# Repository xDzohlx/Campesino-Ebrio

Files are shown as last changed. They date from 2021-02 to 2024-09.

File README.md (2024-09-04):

# Campesino-Ebrio Robot de combate de 12 lb. 

Este es el robot mas completo que he desarrollado.

Ha competido en 4 competencias y actualmente es la versión 3 del robot.

Talent land 2019
Primer competencia del campesino
Tryta 2019
Al no recibir mucho daño tecnicamente se volvio a construir y volvio a competir
Motorama robot conflict 2020
Subcampeon del torneo y primer evento internacional donde se compitió
Norwalk Havoc Robot League 6 feb 2021
Tercer lugar de 4 robots inscritos no se tuvo muy buen desempeño
Norwalk Havoc Robot League Junio 2021
Norwalk Havoc Robot League Finalist Diciembre 2021
Motorama Robot Conflict 2022
Norwalk Havoc Robot League Octubre 2023

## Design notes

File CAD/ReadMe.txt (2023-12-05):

No avanzar los estados de reconstrucción. 
A veces la polea grande no se reconstruye correctamente.

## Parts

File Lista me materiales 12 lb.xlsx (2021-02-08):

Parte | Descripcion | Cantidad | Enlace
Motor del arma | Motor de alta velocidad y potencia | 1 | https://hobbyking.com/es_es/turnigy-xk-3665-3190kv-brushless-inrunner.html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
Motor traccion | Motores de baja velocidad y potencia moderada | 2 | https://hobbyking.com/es_es/propdrive-v2-3536a-910kv-brushless-outrunner-motor.html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
Controladora arma | Controladora de alta corriente | 1 | https://hobbyking.com/es_es/turnigy-plush-32-100a-2-6s-speed-controller-w-bec.html
Controladora traccion | Controladora Bheli32 | 1 | https://hobbyking.com/es_es/flycolor-x-cross-bl-32-50a-brushless-esc.html
Bateria | Bateria lipo de 1300mAmp 4s | 2~3 | https://www.agelectronica.com/detalle.php?p=TA-45C-1300-4S1P-XT60
Radio | Clasico i6 | 1 | https://hobbyking.com/es_es/turnigy-tgy-i6-mode-2-afhds-transmitter-and-6ch-receiver.html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
Switch de encedido | Switch fingertech para traccion y radio | 2 | https://www.fingertechrobotics.com/proddetail.php?prod=ft-mini-switch
Cajas de reduccion | Clasicas p60 de banebots | 2 | http://www.banebots.com/product/P61S-44.html
Ruedas | Colson de 4x1/4 | 2 | http://www.banebots.com/product/WC2-4.html

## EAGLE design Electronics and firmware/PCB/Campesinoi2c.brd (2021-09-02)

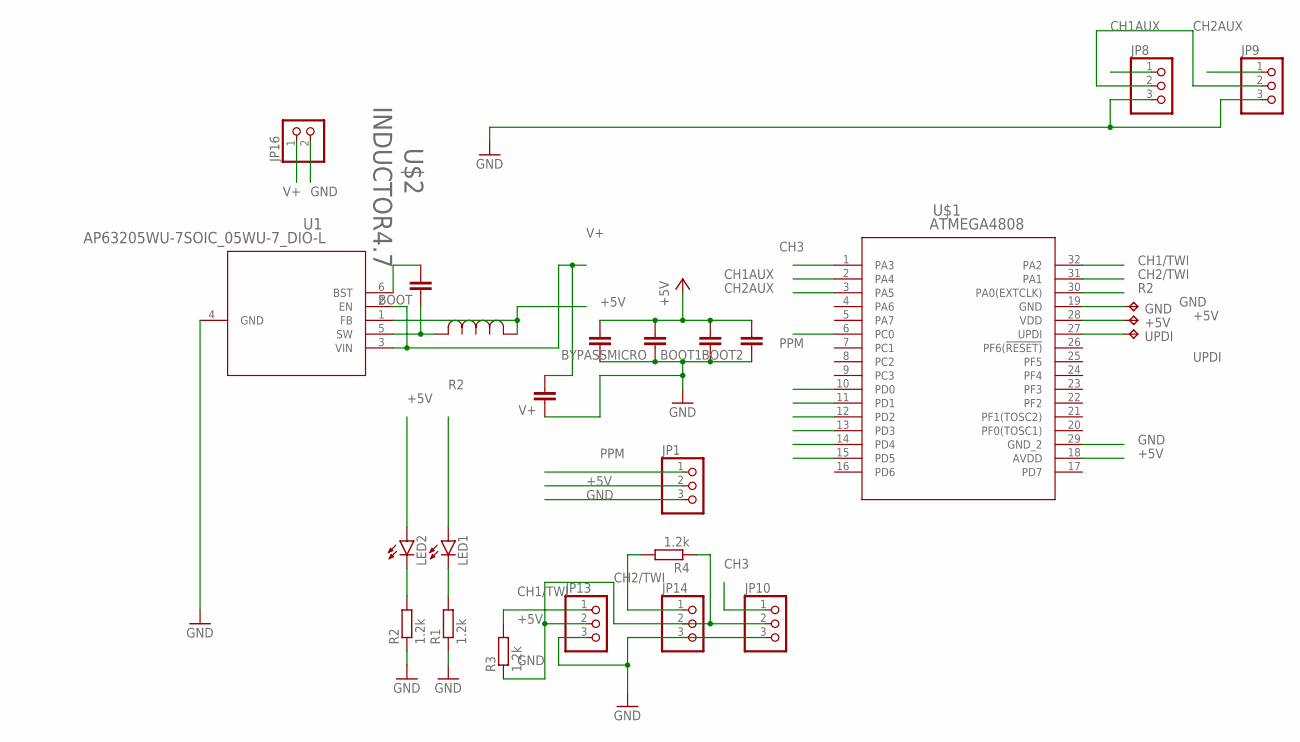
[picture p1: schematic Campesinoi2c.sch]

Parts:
+5V: TPB1,27; B1,27
BOOT, BOOT1, BOOT2: C-EUC0402; C0402
BYPASSMICRO, BYPASSMICRO2: C-EUC0603; C0603
GND: TPB1,27; B1,27
JP1, JP8, JP9, JP10, JP13, JP14: PINHD-1X03_2.54-S; 1X03-S
JP16: PINHD-1X02_2.54-S; 1X02-S
LED1, LED2: LEDCHIPLED_0603; CHIPLED_0603
R1, R2, R3, R4: 1.2k; R0603
U1: AP63205WU-7SOIC_05WU-7_DIO-L; SOIC_05WU-7_DIO-L
U$1: ATMEGA4808; QFP80P900X900X120-32N
U$2: INDUCTOR4.7; IND_NRS5030T100MMGJ_TAY
UPDI: TPB1,27; B1,27
V+: C-EUC1206; C1206

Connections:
+5V: +5V.TP, BOOT1.2, BOOT2.2, BYPASSMICRO.2, BYPASSMICRO2.2, JP1.2, JP8.2, JP9.2, JP10.2, JP13.2, JP14.2, LED2.A, R3.1, R4.1, U1.1 (FB), U$1.18 (AVDD), U$1.28 (VDD), U$2.1
CH1/TWI: JP13.1, R3.2, U$1.32 (PA2)
CH1AUX: JP8.1, U$1.2 (PA4)
CH2/TWI: JP14.1, R4.2, U$1.31 (PA1)
CH2AUX: JP9.1, U$1.3 (PA5)
CH3: JP10.1, U$1.1 (PA3)
GND: BOOT1.1, BOOT2.1, BYPASSMICRO.1, BYPASSMICRO2.1, GND.TP, JP1.3, JP8.3, JP9.3, JP10.3, JP13.3, JP14.3, JP16.2, R1.1, R2.1, U1.4 (GND), U$1.19 (GND), U$1.29 (GND_2), V+.1
unnamed: LED2.C, R2.2
unnamed: LED1.C, R1.2
unnamed: BOOT.1, U1.5 (SW), U$2.2
unnamed: BOOT.2, U1.6 (BST)
PPM: JP1.1, U$1.6 (PC0)
R2: LED1.A, U$1.30 (PA0(EXTCLK))
SENSOR1: U$1.10 (PD0)
SENSOR2: U$1.11 (PD1)
SENSOR3: U$1.12 (PD2)
SENSOR4: U$1.13 (PD3)
SENSOR5: U$1.14 (PD4)
SENSOR6: U$1.15 (PD5)
UPDI: U$1.27 (UPDI), UPDI.TP
V+: JP16.1, U1.2 (EN), U1.3 (VIN), V+.2

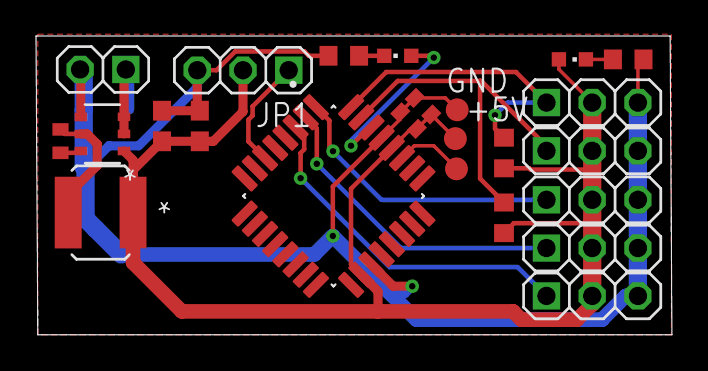
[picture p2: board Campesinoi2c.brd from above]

Board: 2 copper layers, 35.3 x 16.6 mm, 25 parts (1 on the bottom side), 15 nets.

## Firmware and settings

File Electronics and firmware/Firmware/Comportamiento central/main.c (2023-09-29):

/*
	 * Comportamiento central.c
	 *
	 * Created: 06/07/2021 19:38:21
	 * Author : xDzohlx
	 */ 

	#define F_CPU 16000000UL //Frecuencia del cpu 16 MHz
	#define USART0_BAUD_RATE(BAUD_RATE) ((float)(F_CPU * 32 / (16 * (float)BAUD_RATE)) + 0.5)
	#define Kp 32
	#define D 10
	#define acelerador 1
	#define volante 0
	#define arma 3
	#define izquierdo 0
	#define derecho 1
	#define sensor_reversa 4
	#define sensor_acelerometro 5
	#define controlador 3

	#include <avr/io.h>
	#include <avr/interrupt.h>
	#include <avr/cpufunc.h>
	#include <stdbool.h>
	#include <util/delay.h>
	#include <stdio.h>
	
	#define TCB_CMP_EXAMPLE_VALUE   (0x80FF)
	
	void USART0_init(void);
	char USART0_readChar(void);
	//uint8_t softwareid  __attribute__ ((.noinit)) = 0x01;


	uint8_t cont = 0;//Contador de canal
	uint8_t contadc = 0;//Contador de sensores
	uint8_t contador = 0;
	uint8_t programa = 0;
	//uint8_t contfiltro=0;
	
	uint16_t Controlador_D[2] ;
	uint16_t Controlador_P[2] ;
	uint16_t error_anterior = 0;
	volatile uint16_t VALORADC = 0x0000;
	volatile uint16_t canal[7];//valor de canal de 4000 hasta 8000
	//uint16_t canalcal[3][7];//vectores de calibracion
	//uint16_t sensorcal[3][7];
	volatile static uint16_t canalcontrol[2];
	volatile uint16_t sensor[16];
	volatile uint16_t motor[2];//motor 0 izquid, motor 1 derecho
	volatile uint16_t automatico[2];
	volatile uint16_t motor_arma = 0x0000;
	volatile uint8_t contador_pwm_alto = 0x00;
	//volatile uint8_t contador_pwm_bajo = 0x00;
	//RC canales SBUS
	
	volatile static uint8_t sbuschannel[25];
	volatile static uint8_t sbuschannelindex = 0;
	volatile static uint8_t buffer_sbus = 0x00;
	volatile static uint8_t sbus_anterior = 0x00;
	volatile static uint16_t nuevo_canal[25];
	volatile static bool activar_pwm = false;
	
	
	uint16_t controlautomatico[2];
	uint16_t controlautomaticoprevio[2];
	uint16_t canaloffset[2];
	uint16_t sensoroffset[8];
	uint16_t millis[3];
	uint16_t previousmillis = 0;
	uint16_t currentmillis = 0;
	uint16_t nuevomillis = 0;
	uint8_t contfiltro = 0x00;
	uint8_t numsensor = 0;
	char dato_uart = 0x00;
	volatile uint8_t sensorcontrol[2];
	volatile bool manual = true;//0 sin asistencia, 1 asistencia, 2 autonomo
	volatile bool asistido = false;
	volatile bool autonomo = false;
	bool lectura = false;
	bool lectura_canal = false;
	bool sentido = false;
	bool finadelante = false;
	bool fingiro = false;
	volatile bool primero = true;
	volatile bool segundo = true;
	volatile bool tercero = true;
	bool cuarto = false;
	volatile bool reversa = false;
	volatile bool control_reversa = false;

	void offsetsignals(){//etapa de autocalibracion por promedio, pequeño filtro digital
	PORTA.DIRCLR = PIN0_bm;
	PORTF.OUTSET = PIN0_bm|PIN1_bm|PIN2_bm|PIN3_bm;
		while (!lectura_canal&&canal[acelerador]<6500&&canal[acelerador]>5500&&canal[volante]<6500&&canal[volante]>5500){//Seguridad
		}
		_delay_ms(1500);
		for (int i = 0;i<8;i++){//adquisición de señales, 8 valores en total
			_delay_ms(20);
			canaloffset[volante] += canal[volante];
			canaloffset[acelerador] += canal[acelerador];
			sensoroffset[sensor_acelerometro] += sensor[sensor_acelerometro];
		}
		sensoroffset[sensor_acelerometro] = (sensoroffset[sensor_acelerometro]>>3);
		canaloffset[volante] = (canaloffset[volante]>>3);//division del promedio
		canaloffset[acelerador] = (canaloffset[acelerador]>>3);
	PORTF.OUTCLR = PIN0_bm|PIN1_bm|PIN2_bm|PIN3_bm;
	PORTA.DIRSET = PIN0_bm;
	}
	//generador de trayectorias, falta el parametro de velocidad mientras tanto sera fija
	//valores de 4000 a 2000
	uint16_t adelante(uint16_t distancia, uint16_t velocidad){//control de aceleracion de 2000, 2000 max
		if (segundo){
			millis[acelerador] = 0;// reiniciar temporizador
			segundo = false;
		}
			if (millis[acelerador]<=velocidad){//rampa positiva
				controlautomatico[acelerador] = canaloffset[acelerador]+millis[acelerador];
				//controlautomaticoprevio[acelerador] = controlautomatico[acelerador];
			}
		if (millis[acelerador]>=(distancia<<1)){
				contador++;
				segundo = true;
		}
		return  controlautomatico[acelerador];
	}
	uint16_t giro(uint16_t distancia,uint16_t velocidad,bool sentido){//true derecha, false izquierda,alrededor de 900 son 90 grados con 550 de velcodiad tangencial y 500 de giro
				if (primero){
					millis[volante] = 0;// reiniciar temporizador
					primero = false;
				}
				if (millis[volante]>=(distancia)){
					if (controlautomatico[volante]<= canaloffset[volante]){//saturacion
						controlautomatico[volante] = canaloffset[volante];
						}else{
							if(sentido){
						controlautomatico[volante] = (controlautomaticoprevio[volante]<<1)-canaloffset[volante]-millis[volante];//rampa inversa
							}else{
						controlautomatico[volante] = (controlautomaticoprevio[volante]<<1)-canaloffset[volante]+millis[volante];//rampa inversa		
							}
					}
					}else{
					if (millis[volante]<=velocidad){//rampa positiva
						if (sentido){
						controlautomatico[volante] = canaloffset[volante]+millis[volante];
						} 
						else{
						controlautomatico[volante] = canaloffset[volante]-millis[volante];
						}
						controlautomaticoprevio[volante] = controlautomatico[volante];
					}
				}
				if (millis[volante]>=(distancia<<1)){
				controlautomatico[volante] = canaloffset[volante];
				contador++;
				primero = true;
				}
				return  controlautomatico[volante];
	}	
	void ocho(void){
		if (contador==0){
			canalcontrol[volante] = canaloffset[volante];
			canalcontrol[acelerador] = adelante(2000,500);
		}
		if (contador==1){
			canalcontrol[volante] = giro(910,500,false);
		}
		//if (contador==2){
			//canalcontrol[volante] = canaloffset[volante];
			//canalcontrol[acelerador] = adelante(450,450);
		//}
		//if (contador==3){
			//canalcontrol[volante] = giro(2000,500,false);
		//}
		if (contador>=2){
			contador = 0;
		}
	}
	void busqueda(void){
		if (contador==0){
			canalcontrol[volante] = canaloffset[volante];
			canalcontrol[acelerador] = adelante(1000,700);
		}
		if (contador==1){
			canalcontrol[volante] = giro(1200,100,true);
		}
		if (contador>=2){
			contador = 0;
		}
	}
	
	char USART0_readChar(void)
	{
		while (!(USART0.STATUS & USART_RXCIF_bm))
		{
			;
		}
		return USART0.RXDATAL;
	}
	
	void USART1_init(void)
	{
		//PORTA.DIR &= ~PIN1_bm;
		//PORTC.DIR |= PIN0_bm;
		
		USART1.BAUD = (uint16_t)USART0_BAUD_RATE(100000);

		USART1.CTRLA |= USART_RXCIE_bm;

		USART1.CTRLB |= USART_RXEN_bm;
		
		USART1.CTRLC |= USART_PMODE_EVEN_gc|USART_SBMODE_2BIT_gc;
	}
	
 void USART0_sendChar(char c)
	{
		while (!(USART0.STATUS & USART_DREIF_bm))
		{
			;
		}
		USART0.TXDATAL = c;
	}
	
void USART0_init(void)
{
	PORTA.DIR |= PIN0_bm;
	
	USART0.BAUD = (uint16_t)USART0_BAUD_RATE(9600);
	
	USART0.CTRLB |= USART_TXEN_bm;
	
}
	
	void setup(void){
	
		//Configuracion de CLKPER para fuente de reloj de varios perifericos
		ccp_write_io((void *) & (CLKCTRL.MCLKCTRLB), (CLKCTRL_PDIV_2X_gc|CLKCTRL_PEN_bm));//Maxima frecuencia de lectura de pwm en señal de reloj per
			//RTC Reloj de tiempo real
		//while((RTC.STATUS > 0x00 )){}//se checa que no se este uitilizando	el RTC
		//RTC.PER = 0x01A4;//Timer para apagar sistemas autonomos en 7 minutos
		//RTC.CLKSEL = RTC_CLKSEL_INT32K_gc;
		//RTC.DBGCTRL |= RTC_DBGRUN_bm;
		//RTC.CTRLA = RTC_PRESCALER_DIV32768_gc| RTC_RTCEN_bm| RTC_RUNSTDBY_bm;
		//RTC.INTCTRL |= RTC_OVF_bm;//RTC_CMP_bm;
		//configuracion de puertos
		
		PORTA.DIRSET = PIN0_bm|PIN1_bm|PIN0_bm|PIN2_bm|PIN3_bm;//PIN1_bm|PIN0_bm|PIN4_bm|PIN5_bm|PIN6_bm|PIN7_bm;//dirección de entrada en este caso es de salida
		//PORTA.DIRCLR = PIN1_bm;
		PORTF.DIRSET = PIN0_bm|PIN1_bm|PIN2_bm|PIN3_bm;
		
		
		//TCB0.CTRLA |= TCB_ENABLE_bm|TCB_CLKSEL_CLKDIV2_gc;//ACTIVACION DE EVENTOS RELOJ PROVIENE DE TCA A 1MHZ //clkper 
		//TCB0.CTRLB |= TCB_CNTMODE_FRQ_gc;//modo de lectura de frecuencia
		//TCB0.EVCTRL |= TCB_CAPTEI_bm|TCB_EDGE_bm;//ACTIVA CAPTURA DE EVENTOS, EDGE es el sentido del pulso en este caso esta inverso
		//TCB0.INTCTRL |= TCB_CAPT_bm;
		//TCB1.CTRLB |= 0;//modo de tiempo fuera

		TCB0.CTRLA |= TCB_ENABLE_bm;
		TCB0.CCMP = 0xFA0;//Valor top 4000 interrupcion cada milisegundo
		TCB0.INTCTRL |= TCB_CAPT_bm;//habilita la interrupcion	
		
	
		//Interrupcion para perifericos de baja velocidad
		TCB2.CTRLA |= TCB_ENABLE_bm|TCB_CLKSEL_CLKDIV2_gc;
		TCB2.CCMP = 0xFFFE;//Valor top 4000 interrupcion cada 10 milisegundos
		TCB2.INTCTRL |= TCB_CAPT_bm;//habilita la interrupcion
		//USART SBUS PARA RC
		USART0_init();
		USART1_init();
		//CONFIGURACION DE RED DE EVENTOS
		//Configuracion de sistema de eventos para el radio
		EVSYS.CHANNEL2 |= EVSYS_GENERATOR_PORT0_PIN0_gc;//PORTC0 CONECTADO A CANAL 2 para lectura de ppm
		
		EVSYS.USERTCB0 |= EVSYS_CHANNEL_CHANNEL2_gc;//usuario TCB0 conectado al canal 2
		//Configuracion de sistema de eventos para sensor de reversa con filtro
		EVSYS.CHANNEL0 |= EVSYS_GENERATOR_PORT0_PIN3_gc;//PORTA3 conectado a canal 0 para sensor de reversa
		EVSYS.USERTCB1 |= EVSYS_CHANNEL_CHANNEL0_gc;//TCB1 coneectado al canal 0
		//ADC y Vref
		VREF.CTRLA = VREF_ADC0REFSEL_2V5_gc;// Se selecciona la referencia a 2.5 volts par mejorar la resolucion de los sensores
		//ADC con referencia interna
		ADC0.CTRLA |= ADC_RESSEL_bm|ADC_FREERUN_bm;//RESOLUCION Y MODO DE MUESTRAS CONSECUTIVAS
		ADC0.CTRLB |= ADC_SAMPNUM_ACC32_gc;//MUESTRAS
		ADC0.CTRLC |= ADC_REFSEL_INTREF_gc|ADC_PRESC_DIV8_gc;//VOLTAJE DE REFERENCIA
		ADC0.CTRLD |= ADC_INITDLY_DLY16_gc;//CONFIGURACION DEL RELOJ DEL ADC
		//Canales de 0 al 7 despues a partir del 12 o 0x0C
		ADC0.MUXPOS = 0x00;//SELECCION DE CANAL DE ADC PD1
		ADC0.INTCTRL |= ADC_RESRDY_bm;//Habilitar interrupciones de resultado completo
		//ADC0.INTCTRL |= ADC_WCMP_bm;
		ADC0.CTRLA |= ADC_ENABLE_bm;//ENCENDIDO DE ADC
		ADC0.COMMAND |= ADC_STCONV_bm;//INICIO DE MUESTRAS

		
		//timer TCA
		TCA0.SINGLE.CTRLA |= TCA_SINGLE_CLKSEL_DIV1_gc;//fuente de reloj,
		TCA0.SINGLE.PER = 0x07FF;//Selección de resolucion de pwm y periodo total de pwm
		TCA0.SINGLE.CTRLB |= TCA_SINGLE_CMP2_bm|TCA_SINGLE_CMP1EN_bm|TCA_SINGLE_WGMODE_SINGLESLOPE_gc;//Habilitar comparador y seleccion de modo de de generacion de onda con modo de rampa sensilla
		TCA0.SINGLE.CMP1 = 0x3E0;//registro de 16 bits para comparacion y pediodo de pwm
		TCA0.SINGLE.CMP2 = 0x3E0;
		
		TCA0.SINGLE.CTRLA |= TCA_SINGLE_ENABLE_bm;//Habilitar pwm


		//Timer para servo
		TCB1.CTRLA |= TCB_ENABLE_bm;
		TCB1.CCMP = 0xFA0;
		TCB1.INTCTRL |= TCB_CAPT_bm;//habilita la interrupcion
		    
		    

		//configuracion de vector de interrupcion
		CPUINT.LVL0PRI = ADC0_RESRDY_vect_num;
		CPUINT.LVL1VEC = TCB1_INT_vect_num;	
		//Habilitar interrupciones generales
		sei();
		
		_delay_ms(1500);//parpadeo para ver el encendido
		
		offsetsignals();// se obtiene el offset por promedio, de 8 valores por comodidad
		controlautomatico[volante] = canaloffset[volante];
		controlautomatico[acelerador] = canaloffset[acelerador];
		
		//PORTA.OUTSET = PIN0_bm;//Termino la configuracion
	}
	//Interrupción de lectura de RC
	//ISR(TCB0_INT_vect){//Interrupcion de lecutra y decodificacion de ppm
	//if (cont > 0)// lectura del canal no es necesario para decodificador
		//canal[cont -1]=TCB0.CCMP;//lectura del canal no necesario para salida decodificada
		////if (cont==2){
			////PORTA.OUTSET = PIN3_bm;
		////}
		////if (cont==3){
			////PORTA.OUTCLR = PIN3_bm;
		////}
	//cont++;//siguiente canal
	//if (canal[cont-2]>16000)
		//cont = 0;
		//lectura_canal = true;
	//}
	//Interrupción de contador de milisegundos
	ISR(TCB0_INT_vect){//contador de milisegundos, para generador de trayectorias
		millis[acelerador]++;
		millis[volante]++;
		millis[controlador]++;
		TCB0.INTFLAGS &= ~TCB_CAPT_bp;

	}
	
	ISR(TCB1_INT_vect){//decoficador emulado servo
		contador_pwm_alto++;
		if (activar_pwm)
		{
			PORTA.OUTCLR = PIN3_bm;
			TCB1.CCMP = 0xFA0;
			activar_pwm = false;
			contador_pwm_alto = 0x00;
		}
		if (contador_pwm_alto==10)
		{
			PORTA.OUTSET = PIN3_bm;
			TCB1.CCMP = (canal[arma]<<3)+4000;			
			activar_pwm = true;
		}

		TCB1.INTFLAGS &= ~TCB_CAPT_bp;
	}
	//Interrupción periodica de 16 milisegundos para lecturas lentas
	ISR(TCB2_INT_vect){//Interrupcion para checar canales cada 10 ms

		//Sensor de reversa con filtro
			if (sensor[sensor_reversa]>180){
			if (contfiltro<15){
			contfiltro++;
			}
			}
			if (sensor[sensor_reversa]<140){
			if (contfiltro>0){
			contfiltro--;
			}
			}
			if (contfiltro>10){	
				control_reversa = false;
				//PORTA.OUTSET = PIN0_bm;
			}
			if (contfiltro<5){	
				control_reversa = true;
				//PORTA.OUTCLR = PIN0_bm;
			}
		if (canal[4]<5000){
		manual = true;
		asistido = false;
		autonomo = false;
		primero = true;
		segundo = true;
		tercero = true;
		cuarto = false;
		//PORTA.OUTCLR= PIN0_bm;//led de aviso//descomentar despues
		}
		
		if (canal[4]<6500&&canal[4]>5500){
			manual = false;
			asistido = true;
			autonomo = false;
			currentmillis = millis[acelerador];
			if (currentmillis - previousmillis >= 250) {
				previousmillis = currentmillis;
				//PORTA.OUTTGL = PIN0_bm;
			}
		}
		
		if (canal[4]>7000){
		manual = false;
		asistido = false;
		autonomo = true;
			//PORTA.OUTSET = PIN0_bm;
		}
		TCB2.INTFLAGS &= ~TCB_CAPT_bp;
	}
	//Interrupción de lectura de ADC para sensores
	ISR(ADC0_RESRDY_vect){//solo 4 sensores para empezar
	//Canales de 0 al 7 despues a partir del 12 hasta sensor 14
		sensor[contadc-1] = ADC0.RES>>5;//Promedio de 16 muestras
		contadc++;
	if (contadc>= 8){
		contadc = 0;
		lectura = true;
		}
	ADC0.MUXPOS = contadc;
	}
	//Interrupcion USART
	ISR(USART1_RXC_vect){
		
		buffer_sbus = (uint8_t)USART1.RXDATAL;
		sbuschannelindex++;
		if((buffer_sbus == 0x0F)&&(sbus_anterior== 0x00)){
			sbuschannelindex = 0x00;
		}
		sbuschannel[sbuschannelindex] = buffer_sbus;
		if (sbuschannelindex==2)//canal 1
		{
			canal[volante] = sbuschannel[1] + ((sbuschannel[2]&0x07)<<8);//offset de 500 para valor medio
		}
		if (sbuschannelindex==3)//canal 2
		{
			canal[acelerador] = ((sbuschannel[3]&0x3F)<<5) + ((sbuschannel[2]&0xF8)>>3);//offset de 500 para valor medio
		}
		if (sbuschannelindex==4)//canal 3
		{
			canal[arma] = (sbuschannel[3]&0x03)+(sbuschannel[4]<<2)+((sbuschannel[5]&0x01)<<10);
		}
		sbus_anterior = buffer_sbus;
		//nuevo_canal[sbuschannelindex] = sbuschannel[sbuschannelindex];
	}
	//Interrupción de reloj de tiempo real de seguridad
	//ISR(RTC_CNT_vect){//Interrupcion por tiempo seguridad
		////Apagar motores
		//TCA0.SINGLE.CMP1 = canaloffset[acelerador];
		//TCA0.SINGLE.CMP2 = canaloffset[acelerador];
		//while(1){
		//PORTA.OUTTGL = PIN0_bm;//led de aviso
		//_delay_ms(1000);
		//}//se detiene el programa
	//}
	
	int main(void){
		setup();
		while (1){
		
		if (1){
			canalcontrol[volante] = canal[volante];// + Controlador_P[0] - Controlador_P [1];
			canalcontrol[acelerador] = canal[acelerador];
			//motor_arma = canal[volante]<<4;
			reversa = false;
		}
		if (0){//autonomo
			//millis[controlador] = 0;
			reversa = control_reversa;
			if (sensoroffset[sensor_acelerometro]<=sensor[sensor_acelerometro]){//valores negativos
				Controlador_P[volante]=sensor[sensor_acelerometro]-sensoroffset[sensor_acelerometro];//Error del controlador
				canalcontrol[volante] = canal[volante]+(Controlador_P[volante]<<4);//canal[volante] + Controlador_P[0] - Controlador_P [1];	
				canalcontrol[acelerador] = canal[acelerador]-(Controlador_P[volante]<<2);	
			}else{// valores positivos
				Controlador_P[volante]=sensoroffset[sensor_acelerometro]-sensor[sensor_acelerometro];//Error del controlador
				canalcontrol[volante] = canal[volante]-(Controlador_P[volante]<<4);//canal[volante] + Controlador_P[0] - Controlador_P [1];	
				error_anterior = Controlador_P[volante];
				canalcontrol[acelerador] = canal[acelerador]-(Controlador_P[volante]<<2);
			}

		}
		
		
		if (0){//asistido
			//canalcontrol[volante] = giro(2800,500);
			//canalcontrol[acelerador] = canaloffset[volante];//adelante(3000,500);//adelante(2000,1000);
			//funcion de trayectoria
			//ocho();
			canalcontrol[volante] = canal[volante];// + Controlador_P[0] - Controlador_P [1];
			canalcontrol[acelerador] = canal[acelerador];
			//motor_arma = canal[volante]+1500;
			reversa = true;
		}
	//Cinematica del robot, valores de 4000 an 8000 con dos variables de control canalcontrol volante y acelerador
	if(1){//reversa con sensor
		if (canalcontrol[volante]>=canaloffset[volante]){
			canalcontrol[volante] = ((canalcontrol[volante]-canaloffset[volante])>>1);//mezcladora
			motor[izquierdo] = (canalcontrol[acelerador]-canalcontrol[volante])+500;
			motor[derecho] = (canalcontrol[acelerador]+canalcontrol[volante])+500;
			}else{
			canalcontrol[volante] = (canaloffset[volante]-canalcontrol[volante])>>1;//mezcladora
			motor[izquierdo] = (canalcontrol[acelerador]+canalcontrol[volante])+500;
			motor[derecho] = (canalcontrol[acelerador]-canalcontrol[volante])+500;
			}}else{//Normal
			if (canalcontrol[volante]>=canaloffset[volante]){
				canalcontrol[volante] = ((canalcontrol[volante]-canaloffset[volante])>>1);//mezcladora
				motor[izquierdo] = (((canaloffset[acelerador]<<1)-canalcontrol[acelerador])-canalcontrol[volante])>>2;//reversa, solo al acelerador
				motor[derecho] = (((canaloffset[acelerador]<<1)-canalcontrol[acelerador])+canalcontrol[volante])>>2;
				}else{
				canalcontrol[volante] = (canaloffset[volante]-canalcontrol[volante])>>1;//mezcladora
				motor[izquierdo] = (((canaloffset[acelerador]<<1)-canalcontrol[acelerador])+canalcontrol[volante])>>2;//reversa, solo al acelerador
				motor[derecho] = (((canaloffset[acelerador]<<1)-canalcontrol[acelerador])-canalcontrol[volante])>>2;
			}}

			if (motor[izquierdo]>0x07E0){//SATURACION DE MOTORES SUPERIOR
				motor[izquierdo] = 0x07E0;
			}
			
			if (motor[derecho]>0x07E0){
				motor[derecho] = 0x07E0;
			}
			
			if (motor[izquierdo]<0x03E8){//SATURACION DE MOTORES INFERIOR
				motor[izquierdo] = 0x03E8;
			}
			
			if (motor[derecho]<0x03E8){
				motor[derecho] = 0x03E8;
			}
			
			TCA0.SINGLE.CMP1 = motor[izquierdo];
			TCA0.SINGLE.CMP2 = motor[derecho];
			
			dato_uart = (char)(canal[volante]<<3);
			
			USART0_sendChar(dato_uart);
			USART0_sendChar('\n');
	}//while(1)
	}//main

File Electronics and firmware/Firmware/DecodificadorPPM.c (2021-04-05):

/*
 * Decodificador ppm.c
 *
 * Created: 02/12/2020 21:44:54
 * Author : Usuario
 */ 

#include <avr/io.h>
#include <avr/interrupt.h>

volatile static uint16_t canal[6];//valor de 11 bits del canal
int cont = 0;//contador de canal incrementa con cada pulso

void setup(void){
	DDRA |= (1<<PORTA1)|(1<<PORTA2);//pines de salida del decodificador
	PCICR |= (1<<PCIE0);//Habilita las interrupciones por cambio de estado en este caso la 0
	PCMSK0 |= (1<<PCINT0);//Habilita el pin 0 de la interrupcion que es el PORTA0
	//Configuracion de timer de 16 bits para lectura de ppm con microsegundos
	TCCR1B = (1<<WGM12)|(1<<CS11);//Seleccion de reloj y forma de donda en este caso sirve para captura
	
	OCR1A = 0xFA0;//valor de sincronizacion
	//Interrupciones
	TIMSK1 = (1<<OCIE1A);//Habilita interrupciones del timer
	
	TCNT1 = 0x0000;//Reinicia el contador
	sei();//Activa interrupciones globales
}
//Interrupcion por cambio de estado para lectura
ISR(PCINT0_vect){
	if (!(PINA & 0x01)){//checa el cambio en el pin si es bajo
		if (cont == 0){//flanco de subida canal 1
			PORTA |= (1<<PORTA1);
		}
		if (cont > 0){// lectura del canal no es necesario para decodificador
			canal[cont -1]=TCNT1;//lectura del canal no necesario para salida decodificada
			PORTA = (PORTA<<1);
		}
		TCNT1 = 0x00;//reinicio del timer del canal
		cont++;//siguiente canal
	}
}
ISR(TIMER1_COMPA_vect){//Segundo vector de interrupcion, sincronizacion
	cont = 0;//reinicia la posicion de los canales
}
int main(void){
	setup();//inizializacion
	while(1){
	}
}

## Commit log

2021-03-10 Add files via upload
    Diseño en solidworks de mi robot el campesino ebrio
    [6-32 bane.SLDPRT, Arma campesino.SLDPRT, Brazos.SLDPRT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]
2021-04-05 Create Lista de material
2021-04-05 Create DecodificadorPPM.c
    Decodificador para receptor de PPM sin PWM. Estsa probado en Norwalk en 6 de febrero de 2021
2021-04-07 Create Cad
2021-04-09 Create PCBS
2021-07-11 Create Comportamiento central.c
    Programa de prueba para sistema autónomo, lectura de señales de entrada y sensores
2021-08-06 Update Comportamiento central.c
    Update sensor to read less sensors, working on mixer for upside down driving
2021-08-06 Working version with flip switch
    [Comportamiento central.c]
2021-08-09 Update reversa y tiempo
    Trabajo en progreso para reversa automática con un filtro y un vector de tiempo en ms, la parte del vector ya funciona a 32 bits pero el switch automatico tiene problemas
    [Comportamiento central.c]
2021-08-14 Prueba
    Prueba exitosa del sistema de conducción asistida los sensores si centran un objeto pero necesitan ser filtrados. Se leen dos sensores y al parecer se necesita un controlador D solo tiene controlador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
2021-08-14 Nuevas piezas mejoradas
    [Costado nuevo.SLDPRT, Costado.SLDPRT]
2021-09-02 Version probada en nueva placa
    Version funcionando los motores con rtc y sensores adc falta generador de trayectorias y planeador de trayectorias
2021-09-04 Seleccion de modo con RC
    Funciona bien la selección pero no funciona al momento de mandar las señales o paro
2021-09-05 Funciona el vector para ir adelante
2021-09-09 Ya gira a la izquierda
2021-09-09 update generador de trayectorias
    Generador de trayectorias actualizado, tiene una funcion para girar a ala izquida y otra a la derecha , ya esta funcionando y esta probado en el robot fura del debug
2021-09-24 Update Comportamiento central.c
    Sensor de reversa funcional
    [Comportamiento central.c]
2021-09-28 Acelerometro mejorado
    Se agrego la característica de sumador del ADC para un promediador del filtro por hardware agregando la asistencia en la conducción pero no esta probado
2021-09-29 Controlador de tracción funcionando
    Controlador de tracción funcionando y sin oscilaciones. Controla aceleración y giro con muy buen desempeño elimina casi totalmente el sobrebirage y es mucho mas facil ir derecho
2022-02-24 Add files via upload
    last version working in NHRL finals and Motorama 2022
2023-07-29 Update to Sbus
    Sbus funcionando a 2 canales falta agregar funcionalidad a la cinematica inversa
2023-08-14 Update main.c
    PWM emulado para arma,
2023-12-05 Delete Cad directory
    New version to be uploaded
    [6-32 bane.SLDPRT, Arma campesino.SLDPRT, Brazos.SLDPRT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]
2023-12-05 Update del cad

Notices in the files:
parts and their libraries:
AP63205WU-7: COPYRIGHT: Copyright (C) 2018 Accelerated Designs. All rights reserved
